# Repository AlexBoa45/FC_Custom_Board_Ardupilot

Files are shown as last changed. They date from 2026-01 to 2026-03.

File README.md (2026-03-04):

# Master Thesis Project, UPC-EETAC: 
# Design and development of the control PCB for a drone with a study of potential space applications

By: Alejandro Boadella

# Content

This TFM (project) is devoted to learning, exploring and expanding knowledge of the basic components essential for creating autonomous devices.

Control and power distribution boards are critical subsystems in unmanned vehicles. This project focuses on the complete design process of a dedicated drone control PCB. Furthermore, it includes a study of potential space applications and their specific technical requirements.

The principal objectives of this TFM are:

- Develop a functional drone control PCB.
- Create the drivers to manage the drone control PCB with ArduPilot.
- Evaluate the current design and expose space requirements.

TFE-Alejandro_Boadella.pdf is the main development document created.

**All the objectives have been accomplished. This project was developed over 5 months and involved the design of my very first PCB. The result is a fully functional PCB that can be used in a drone and has been successfully ported to the ArduPilot firmware. The magnetometer and MicroSD capabilities are not yet functional and require further improvement; however, the remaining sensors and system capabilities are fully operational. The microSD is most probably not operational due to hwdef file definition issues and poor routing, and the magnetometer is not operational due to manufacturer-related problems.**

This repository contains all the documentation developed during the TFM. All the design has been developed in Altium. BOM, CPL, Gerber, Master thesis and additional files can be found in this repository.

***IMPORTANT: TFE-Alejandro_Boadella.pdf schematics (shown pictures) and BOM file contain old HSE clock (incompatible with Ardupilot), functional flight controller version carries ASEMB-24.000MHZ-LC-T HSE clock, not SIT1602-22-33E-26.000000D. Both clocks contain same package. A simple susbtitution is required in BOM for manufacturing. TFE-Alejandro_Boadella.pdf explains this problem too.***

NOTE: the explanation of how to port a custom PCB flight controller to ArduPilot, development of a boards, space analysis and more can be found in the thesis.

## Simple Ardupilot Porting

Watch the video (https://www.youtube.com/watch?v=VTwxMDwfPzs)

## Simple Hardware Explanation

Watch the video (https://www.youtube.com/watch?v=8rlyB9k72sw)

## Here down below, you can see a few images from the developed project:





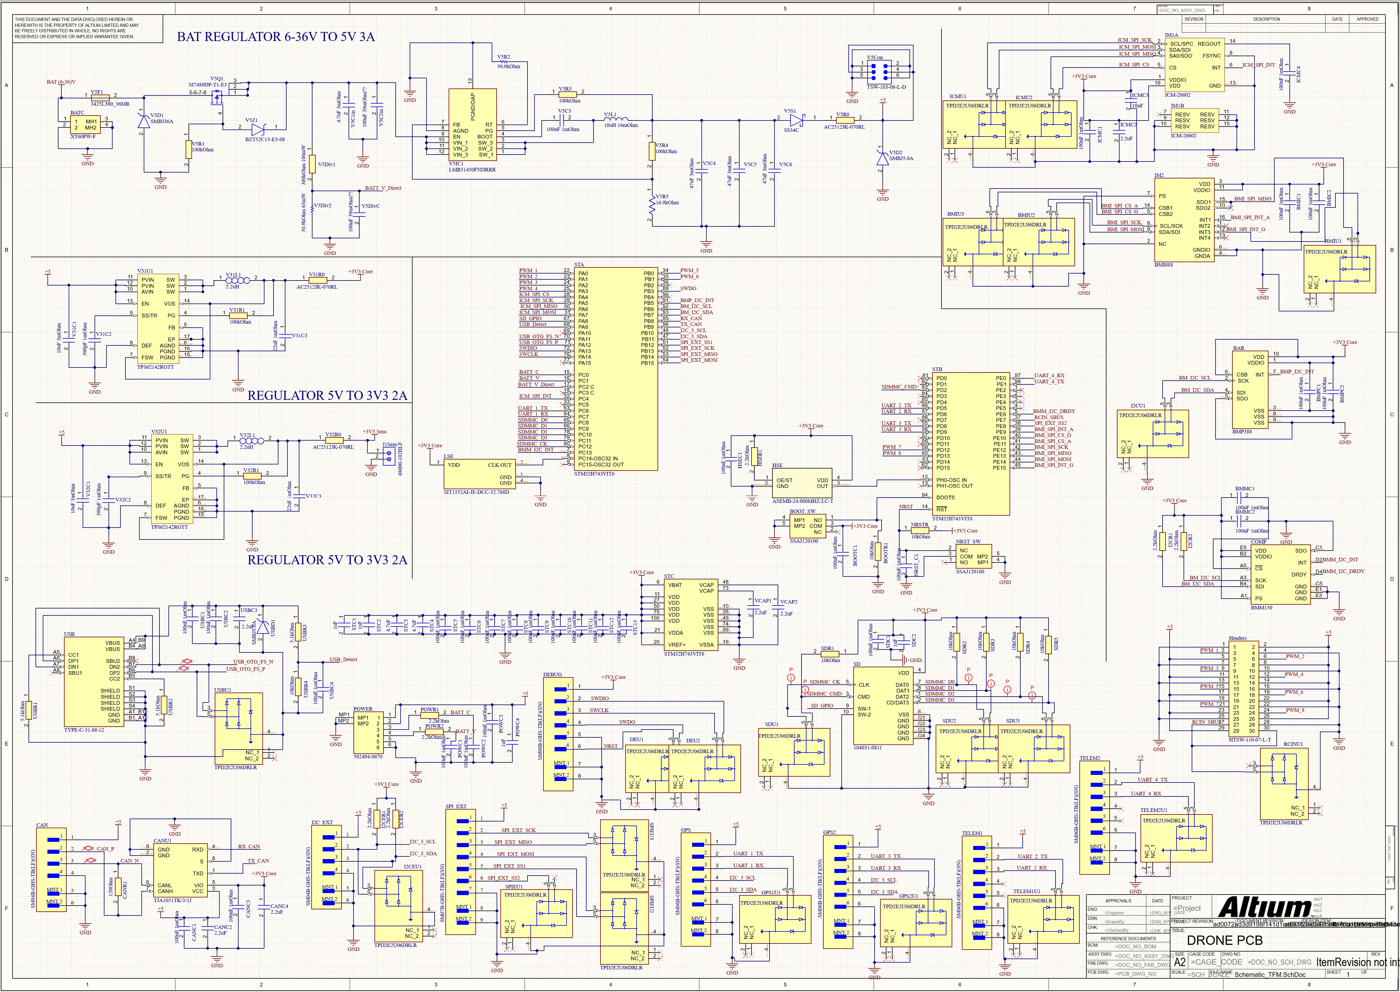
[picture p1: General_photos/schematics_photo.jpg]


## Tests: (autonomous flight has been tested and it actually work, no video has been done tho)

Watch the video (https://youtu.be/3_edOLgjn7w)

Watch the video (https://youtu.be/a62x8s5vOFY)

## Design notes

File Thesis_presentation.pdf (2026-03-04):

# Design and development of the control PCB for a drone with a study of potential space applications

Master's degree in Aerospace Science and Technology (MAST)

Boadella Aguado, Alejandro

Advisor:
- UPC: Oscar Casas Piedrafita
Academic support:
- UPC: Francisco Javier Lopez Garcia and Miguel Valero Garcia

# Index

### 1. Objectives and schedule

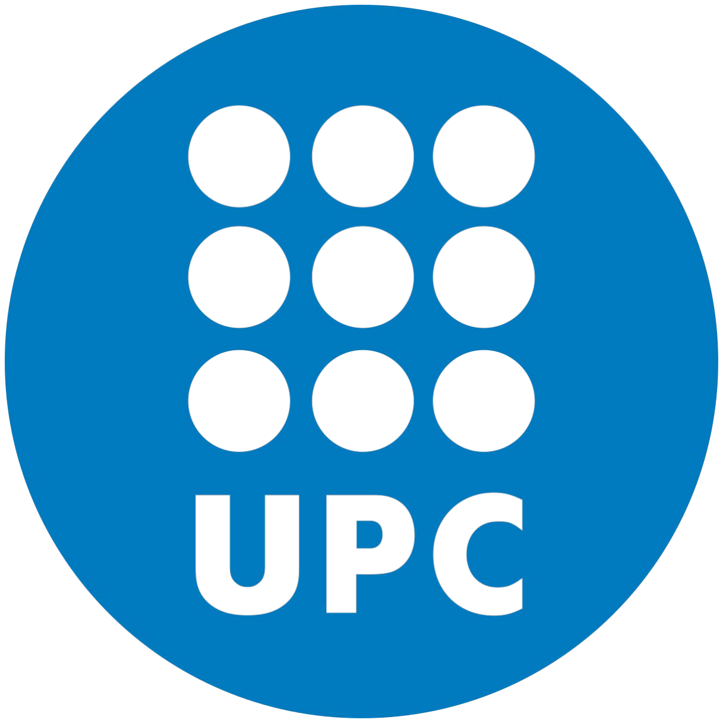
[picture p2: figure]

### 2. Intro and PCB Schematics 3. PCB Routing 4. Manufacturing and PCBA Files 5. Software Porting 6. Space Overview and application 7. Testing 8. Comparison 9. Cost and environment 10. Conclusions

# 1 - Objectives and schedule

# 1 - Objectives and schedule

### - Objectives of the TFM:

- Develop a functional drone control PCB.
- Create the drivers to manage the drone control PCB with ArduPilot.
- Evaluate the current design and expose space requirements.

# 1 - Objectives and schedule

- Example of commercial drone control PCB.

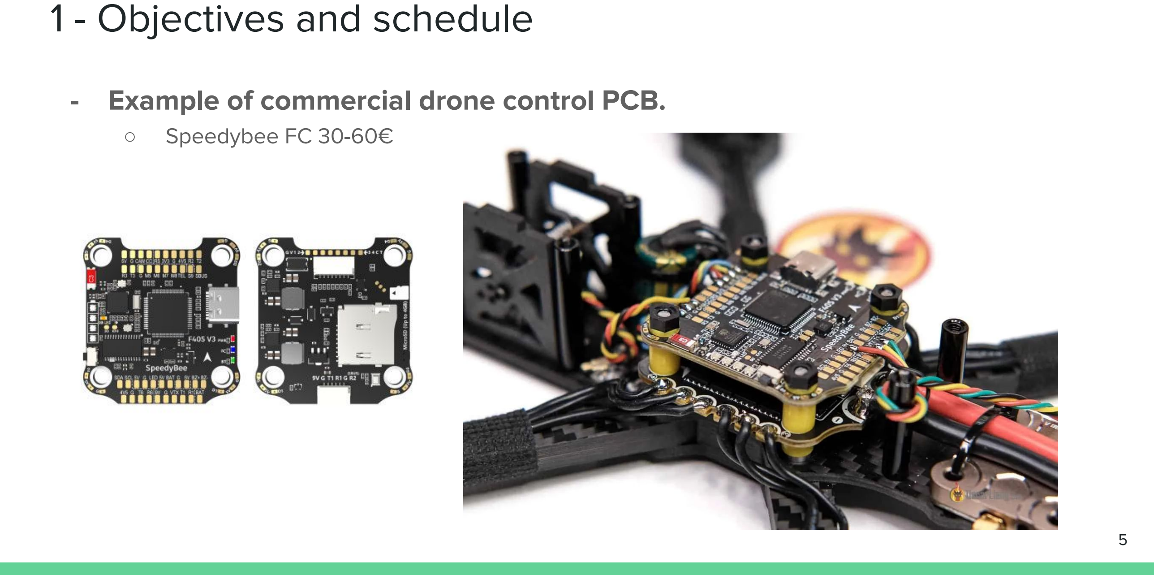
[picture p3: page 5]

- Speedybee FC 30-60€

# 1 - Objectives and schedule

### - Other examples:

- OpenPilot Revolution 60€
- Matek FC H743 70-110€
- Pixhawk 60-100€
- CubePilot Cube Orange/+ 350-600€
- CUAV X7 PRO+ 860€
- Makerfire UTMSYS USX51 600-1000€
OpenPilot | Matek | 6 Pixhawk | CUAV X7
CubePilot | Makerfire

# 2- Introduction

### - Basic components of a FC:

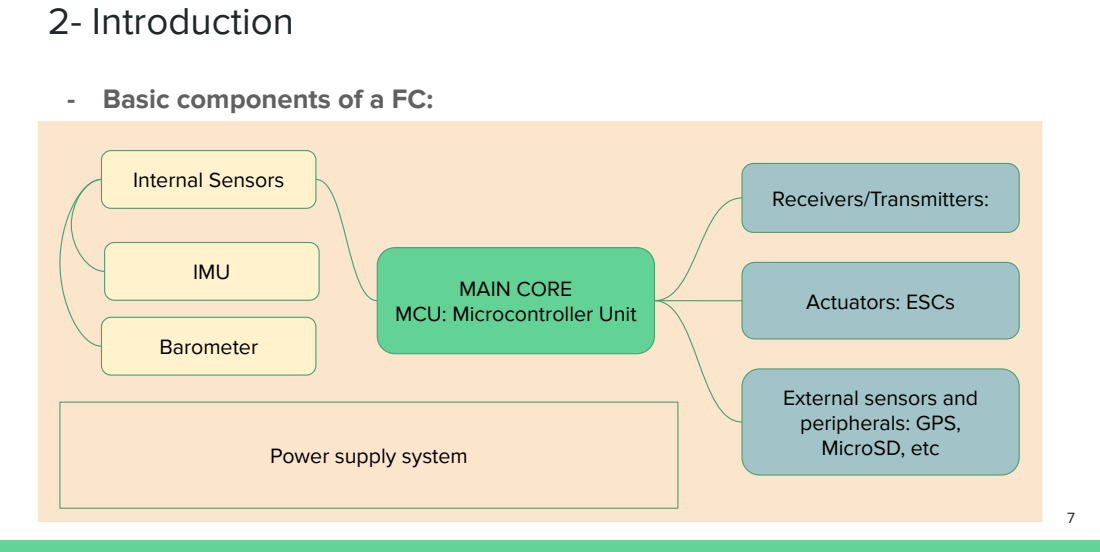
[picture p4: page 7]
Internal Sensors; Receivers/Transmitters:; Actuators: ESCs; IMU; Barometer

MAIN CORE
MCU: Microcontroller Unit

External sensors and
peripherals: GPS,
MicroSD, etc

Power supply system

# 2 - PCB Schematics

### - Before component selection:

- Drone Software: Ardupilot (professional firmware) → relies on ChibiOS.
- ChibiOS is a RTOS (Real Time Operating System).
■ IMPORTANT: Not all sensors and MCUs are supported by default.
- Drone Standard: Pixhawk Standard
■ Pixhawk connector-bus standard applied

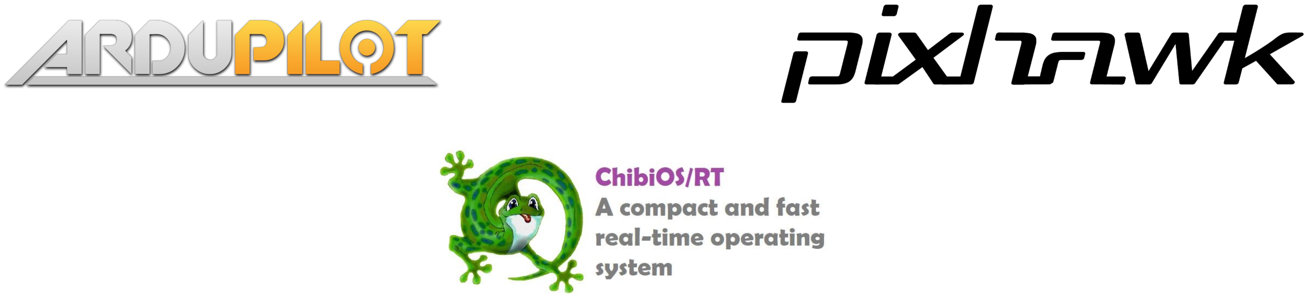
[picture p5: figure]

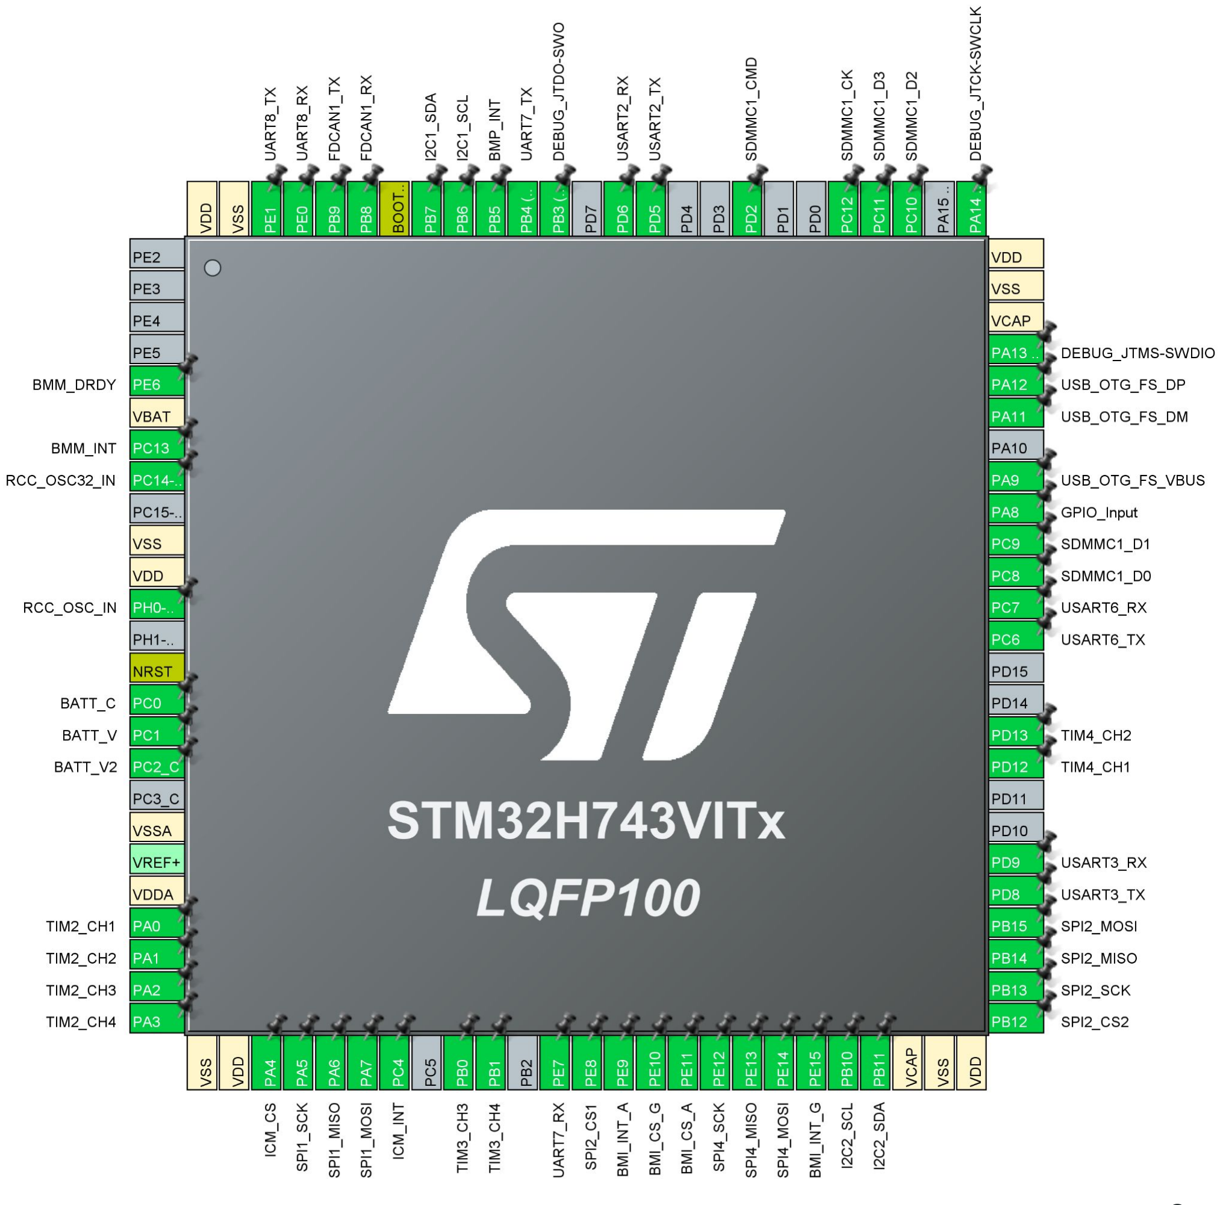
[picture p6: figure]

2 - PCB Schematics - MCU: - | High performance MCU: STM32H743VIT6 ■ | ARM-M7 RISC 480 MHz ■ | 2 MB Flash, 1 MB RAM ■ | LQFP100 (80/100 pins used) ● | 3 SPI (2 internal) ● | 1 SDMMC ● | 2 I2C (1 internal) ● | 3 ADCs (1 internal) ● | 8 PWM ● | 1 CAN ● | 1 USB ● | 1 SWD ● | 4 UART ● | MCU power connections

# 2 - PCB Schematics

### - MCU clock and schematics:

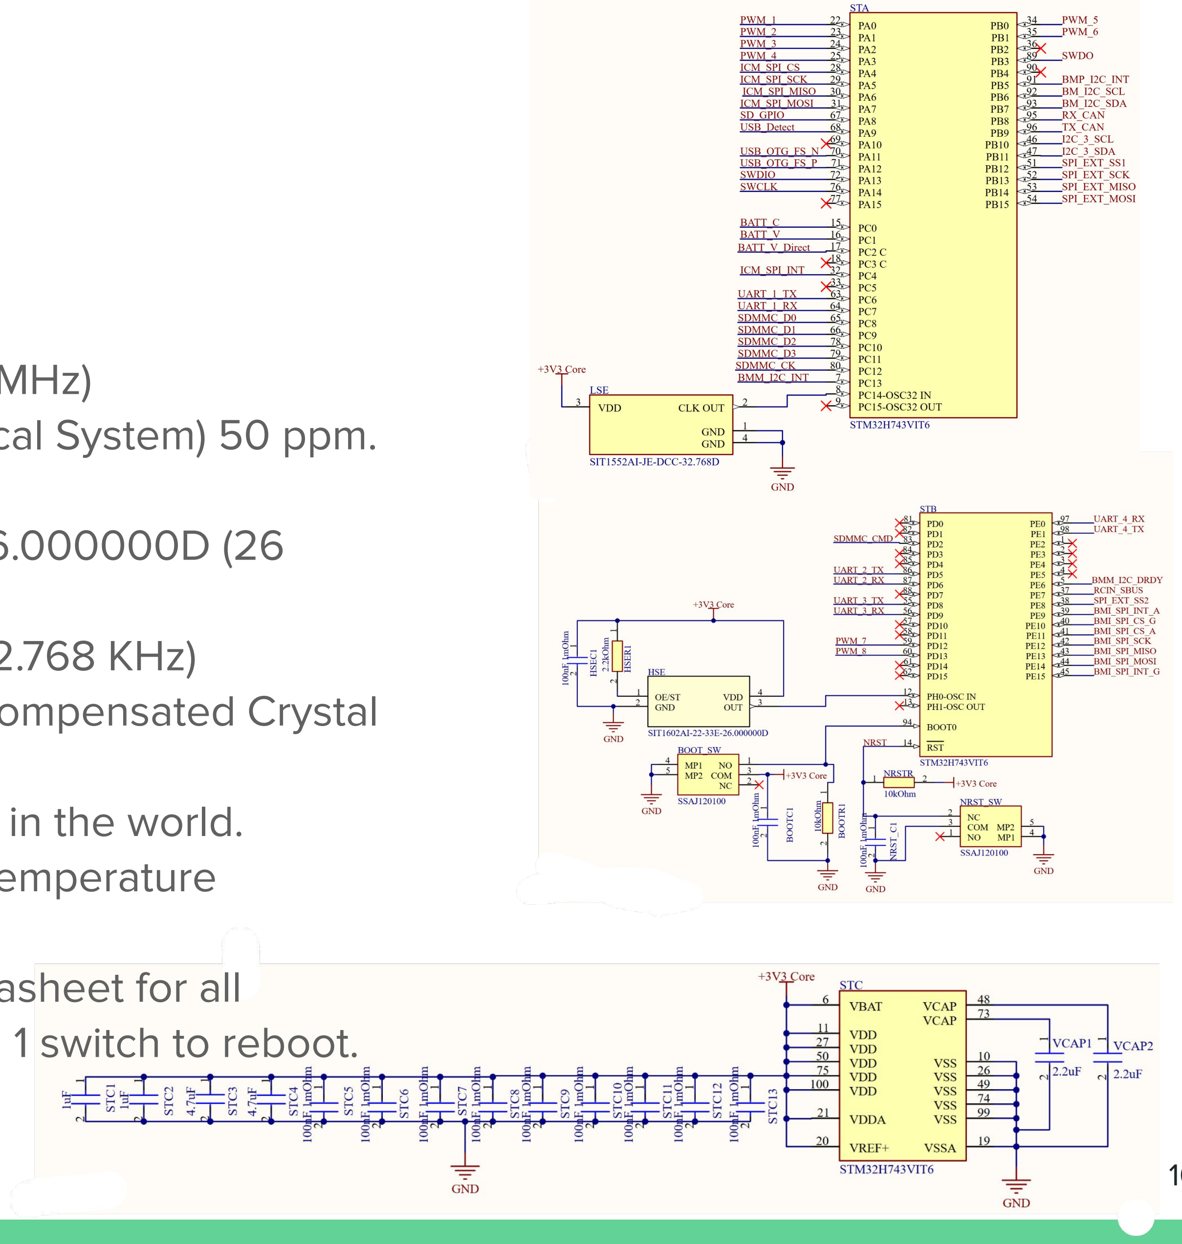
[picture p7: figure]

- HSE: ASEMB-24.000MHZ-LC-T (24 MHz)
■ | MEMS (Micro ElectroMechanical System) 50 ppm.
■ | Good against vibrations.
■ | Previously SIT1602-22-33E-26.000000D (26
| MHz).
- LSE: SIT1552AI-JE-DCC-32.768D (32.768 KHz)
■ | MEMS+TCXO (Temperature Compensated Crystal
| Oscillator) 5 ppm.
■ | Smallest programmable clock in the world.
■ | Good against vibrations and temperature
| variations.
- Conditioning specified as in the datasheet for all components. 1 switch for BOOT and 1 switch to reboot.

# 2 - PCB Schematics

### - Sensors:

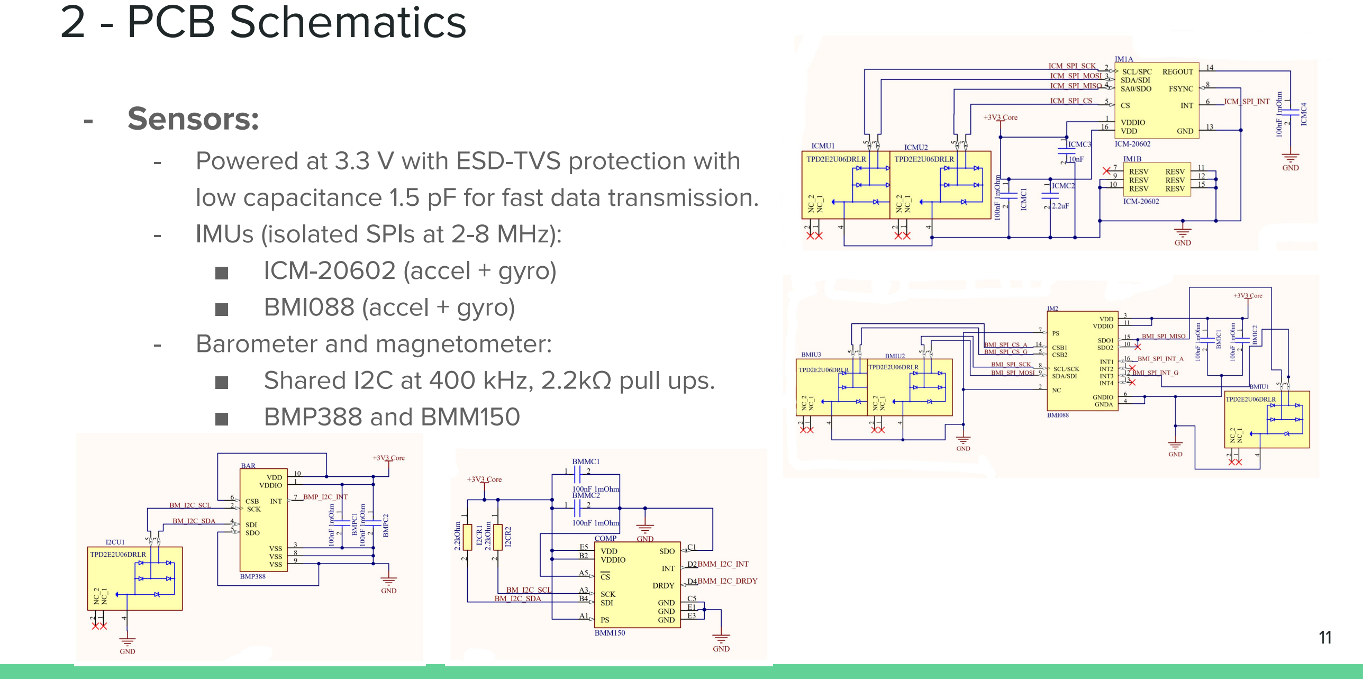
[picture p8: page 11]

- Powered at 3.3 V with ESD-TVS protection with low capacitance 1.5 pF for fast data transmission.
- IMUs (isolated SPIs at 2-8 MHz):
■ | ICM-20602 (accel + gyro)
■ | BMI088 (accel + gyro)
- Barometer and magnetometer:
■ | Shared I2C at 400 kHz, 2.2kΩ pull ups.
■ | BMP388 and BMM150

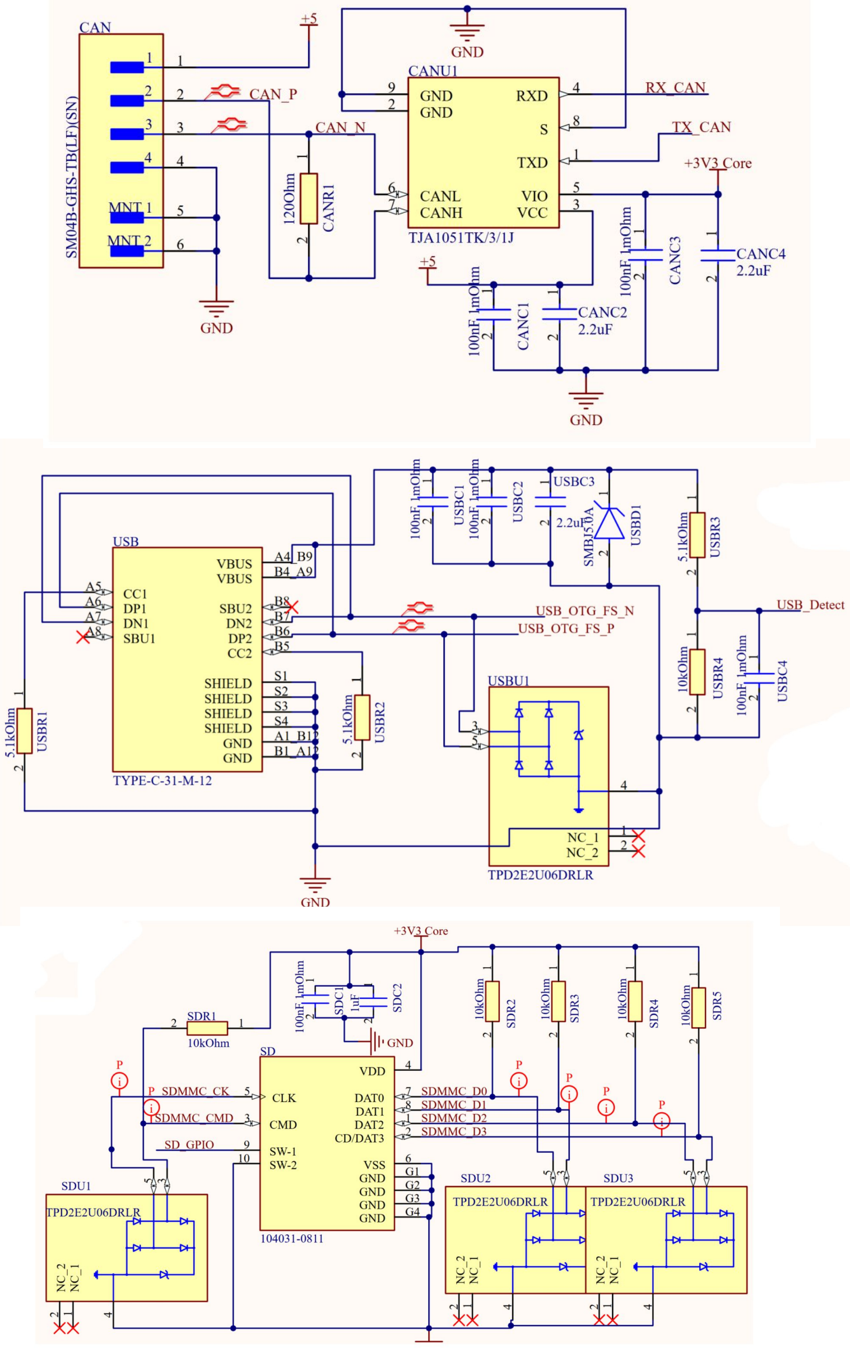
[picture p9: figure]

# 2 - PCB Schematics

### - Complex buses/connectors:

- CAN:
■ | 120 Ω
■ | Pixhawk connector SM04B-GHS JST.
■ | TJA1051TK/3/IJ transceiver (allows 3V3).
- USB 2.0 FS:
■ | 90 Ω
■ | 5.1 kΩ for termination device.
■ | ESD protection + filtering + detection line.
■ | It does not provide power source.
- SDMMC (MicroSD):
■ | 10 kΩ pull ups, except on CK line
■ | ESD protection + filtering + detection line.

# 2 - PCB Schematics

### - Other buses and connectors:

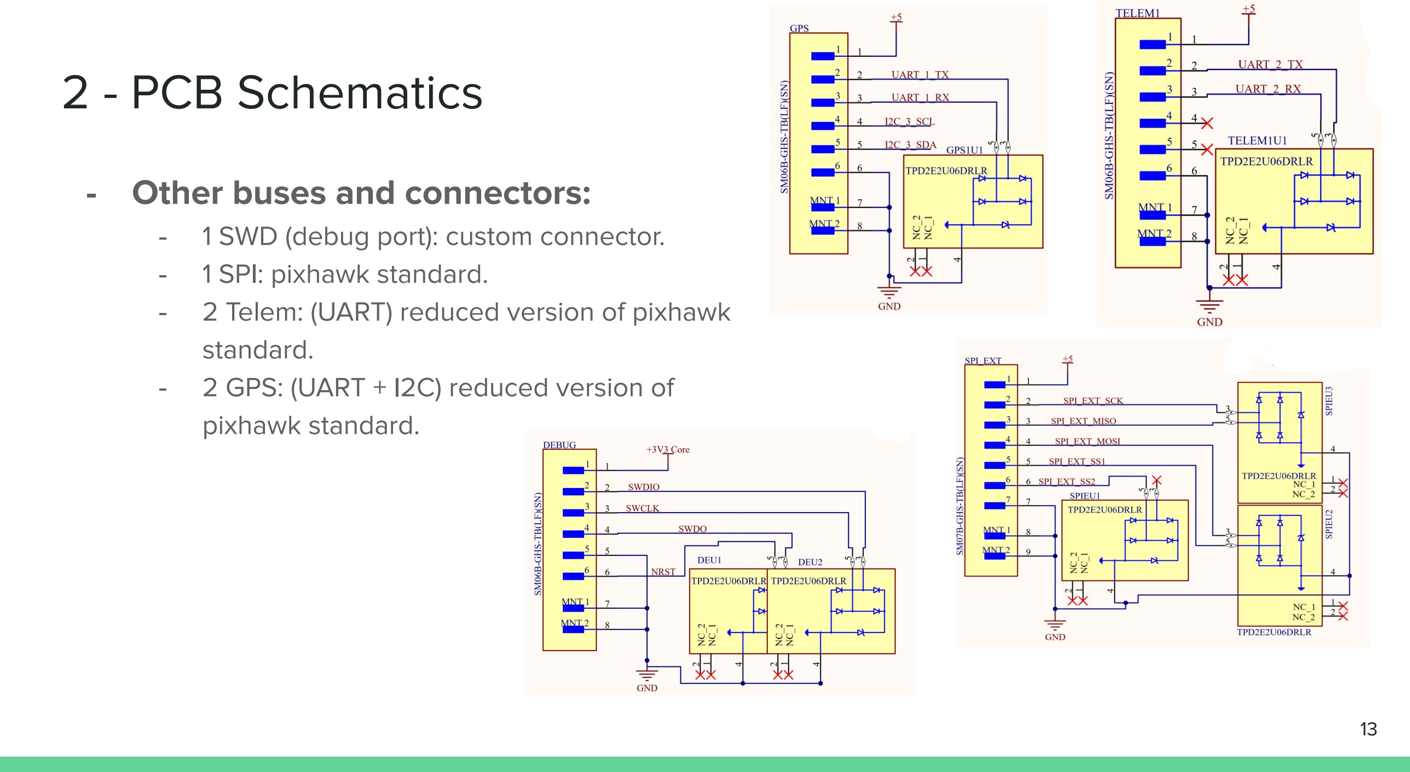
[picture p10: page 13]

- 1 SWD (debug port): custom connector.
- 1 SPI: pixhawk standard.
- 2 Telem: (UART) reduced version of pixhawk standard.
- 2 GPS: (UART + I2C) reduced version of pixhawk standard.

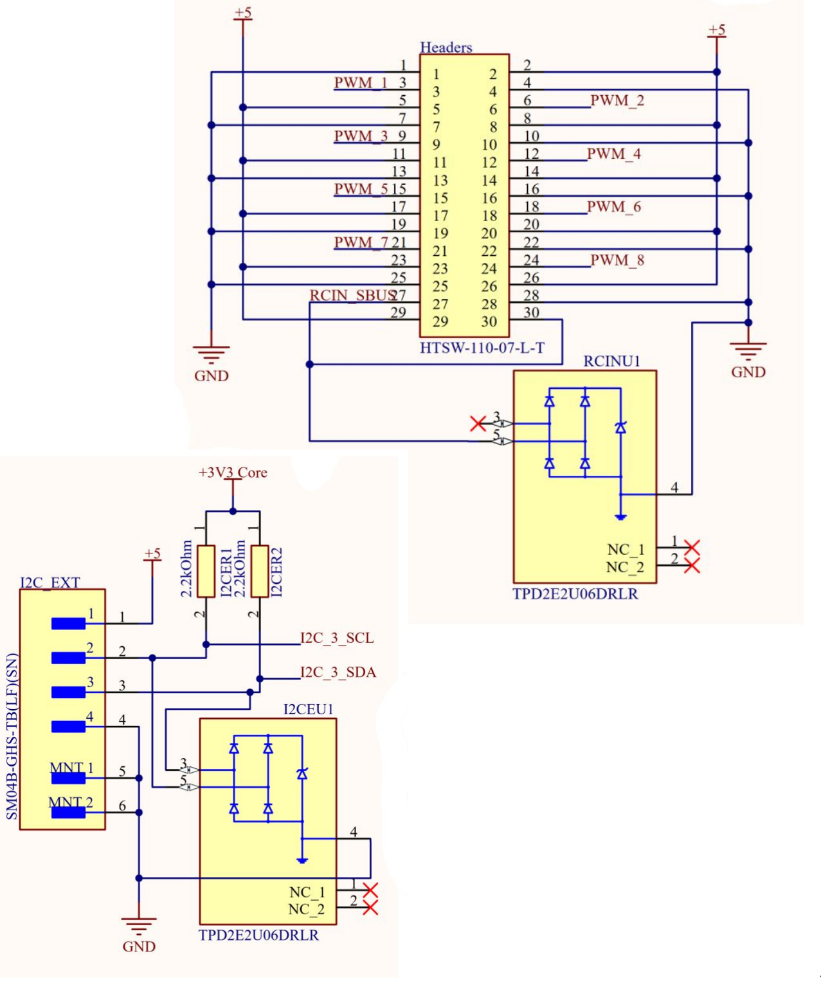
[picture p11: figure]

# 2 - PCB Schematics

### - Other buses and connectors:

- 1 I2C: pixhawk standard.
- 2.54 mm pitch headers/pins:
■ | 8 PWM (No ESD protection and no
| resistance in serie)
■ | 1 RCIN conector (UART RX) (admits
| SBUS with internal inversion).

# 2 - PCB Schematics

### - Power supply system:

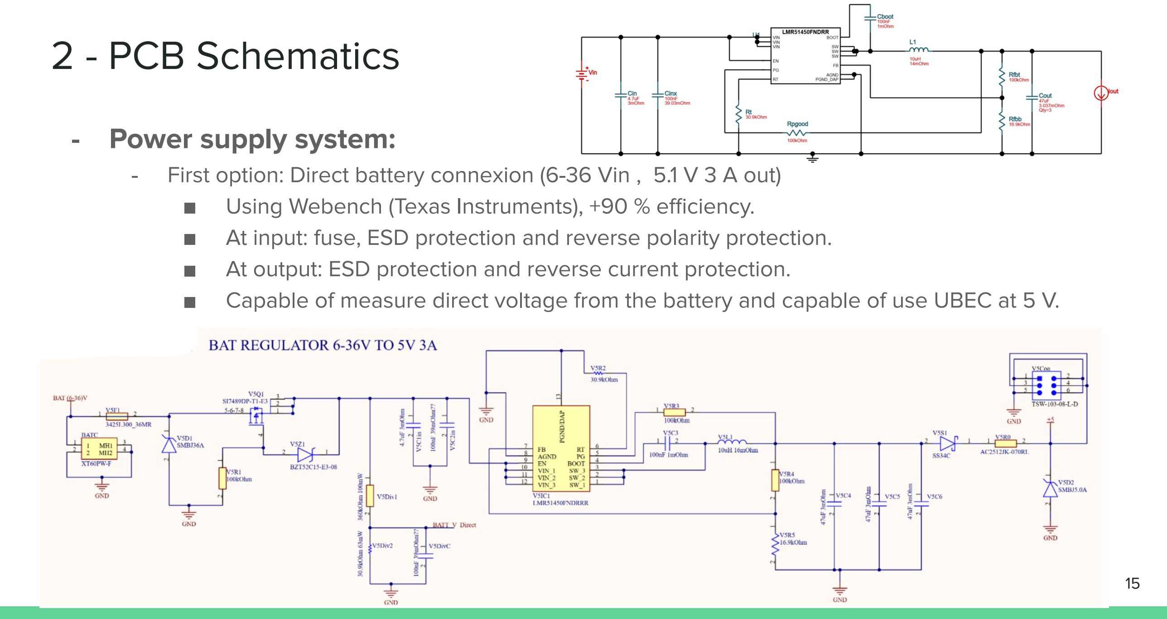
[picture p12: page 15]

- First option: Direct battery connexion (6-36 Vin , 5.1 V 3 A out)
■ | Using Webench (Texas Instruments), +90 % efficiency.
■ | At input: fuse, ESD protection and reverse polarity protection.
■ | At output: ESD protection and reverse current protection.
■ | Capable of measure direct voltage from the battery and capable of use UBEC at 5 V.

# 2 - PCB Schematics

### - Power supply system:

- Second option: Pixhawk battery connexion port
■ | 5.3 V at 2.5 A (real values are near 5.4 V).
■ | Filtered.
■ | Capable of measure current and voltage from external block.

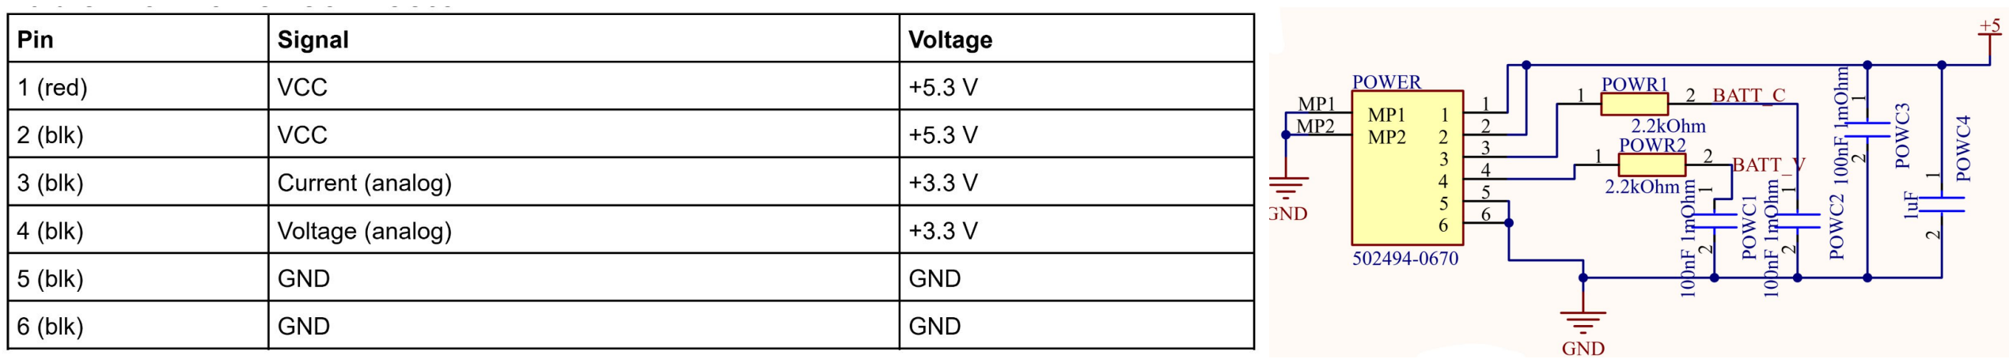
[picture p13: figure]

# 2 - PCB Schematics

### - Power supply system:

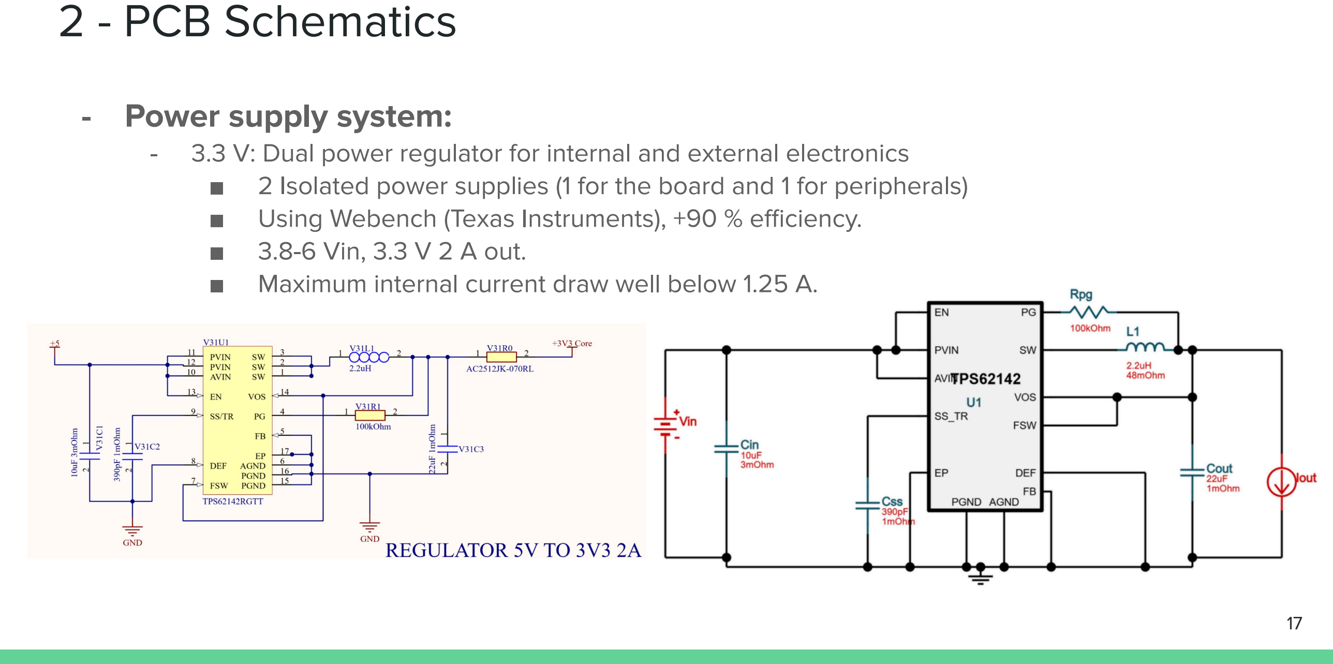
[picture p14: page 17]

- 3.3 V: Dual power regulator for internal and external electronics
■ | 2 Isolated power supplies (1 for the board and 1 for peripherals)
■ | Using Webench (Texas Instruments), +90 % efficiency.
■ | 3.8-6 Vin, 3.3 V 2 A out.
■ | Maximum internal current draw well below 1.25 A.

# 3 - PCB Routing

### - Layer Stackup JLCPCB:

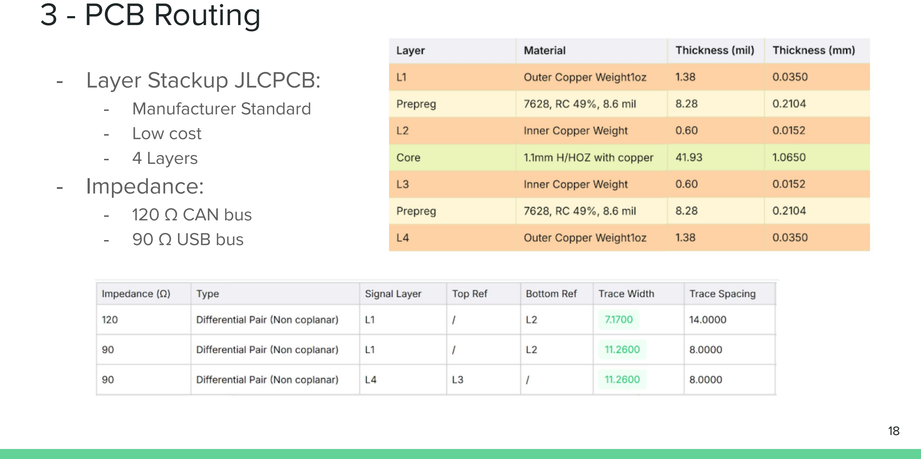
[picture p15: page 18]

- Manufacturer Standard
- Low cost
- 4 Layers

### - Impedance:

- 120 Ω CAN bus
- 90 Ω USB bus

# 3 - PCB Routing

### - Planes and trace width IPC-2152:

- L1: Signal and power lines
- L2: GND → reference plane
- L3: Power (5V and 3V3) and GND → reference
- L4: Signal

# 3 - PCB Routing

### - Power lines:

- Following datasheet routing.

### - Sensors and MCU:

- BMM150 copper pour.
- Capacitors near MCU.
- BMI088, merge MISO lines.
■ Problematic on high-freq.

# 3 - PCB Routing

### - Special buses:

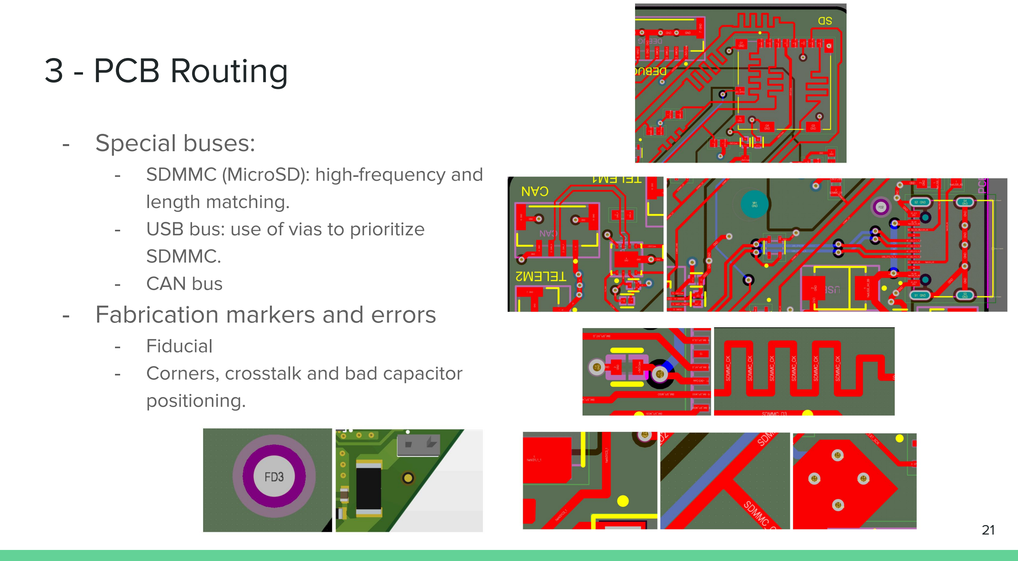
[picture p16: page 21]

- SDMMC (MicroSD): high-frequency and length matching.
- USB bus: use of vias to prioritize SDMMC.
- CAN bus

### - Fabrication markers and errors

- Fiducial
- Corners, crosstalk and bad capacitor positioning.

# 4 - Manufacturing and PCBA Files

- Manufacturer most stringent capability and verification:
- Trace width 4 mil +-20 % (39.37 mil = 1 mm) (specially for magnetometer)
- Un-plug vias for testing and 0402 min size to reduce cost.
- Always checking DFM (Design For Manufacturability).
■ Altium design rule checker and/or Manufacturer programme.
- Actual JLCPCB trace positioning deviation <1 mil. No solderwicking, nor soldebridging.
- Some vias plugged with solder due to HASL bath.

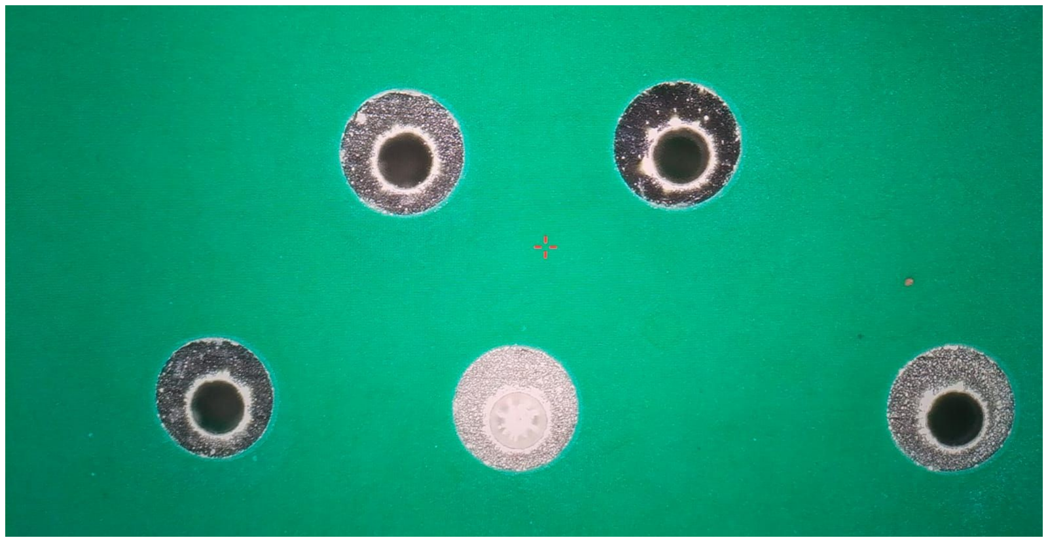
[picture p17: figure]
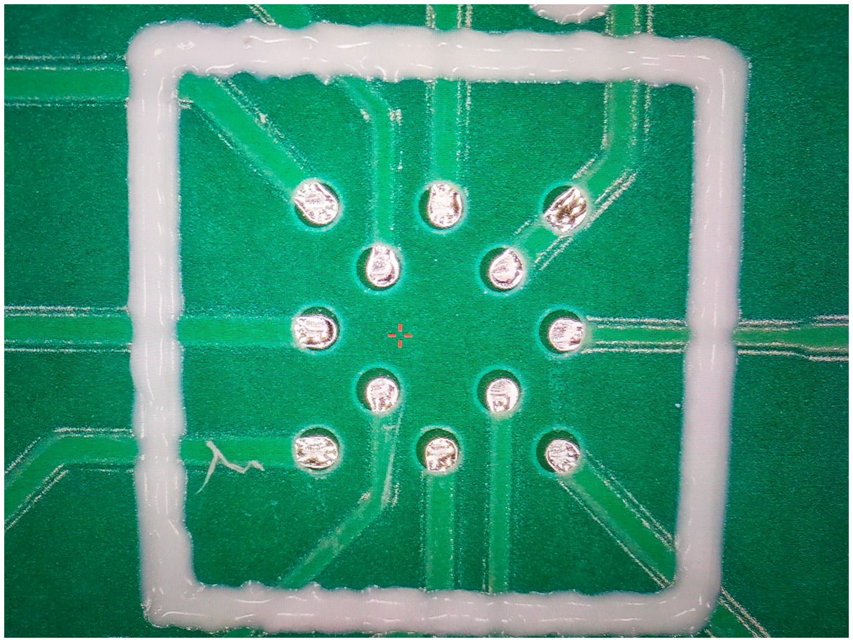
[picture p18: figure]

- Files:
- Gerber X2
- CPL (or PnP): Customized (wrong rotations).
■ 146 components per board.
- BOM: Customized (Manufacturer part number + PCB manufacturer number) ■ 44 different components per board (in fact 50 considering non-used).

# 5 - Software Porting

### - Environment installation:

- Linux and Ubuntu
- Download ArduPilot
- Install ArduPilot and ChibiOS
- Update them

### - Create a folder and add hwdef.dat and hwdef-bl.dat

files.

### - Create the firmware and the

bootloader.

wsl --install
wsl --install -d Ubuntu
sudo apt update && sudo apt install git -y

git clone https://github.com/ArduPilot/ardupilot.git

cd ardupilot
git submodule update --init --recursive Tools/environment_install/install-prereqs-ubuntu.sh -y . ~/.profile

cd ardupilot/libraries/AP_HAL_ChibiOS/hwdef

cd ~/ardupilocd
ardupilot/libraries/AP_HAL_ChibiOS/hwdeft ./Tools/scripts/build_bootloaders.py CustomH7 ./waf configure --board CustomH7
./waf copter

# 5 - Software Porting

- 2 MB in order:
- Divided in 16 pages of 128 KB
- Bootloader 128 KB
- Dedicated storage 32 KB
- Firmware + addons 1888 KB
- hwdef.dat and hwdef-bl.dat files:
- Test-fail-read_doc-try_again
- PLL with 26 MHz HSE:
- In STM32cubeIDE impossible with auto-mode, possible with manual mode with multipliers/dividers.
- ChibiOS needs 24 MHz , (Impossible to interact with manual PLL values at 26 Mhz, I tried, plausible reason→USB 48 Mhz), (replacement!!).

# Core

MCU STM32H7xx STM32H743xx
FLASH_SIZE_KB 2048
FLASH_RESERVE_START_KB 128 …
# Clock

OSCILLATOR_HZ 24000000
STM32_HSE_BYPASS
STM32_LSE_BYPASS
STM32_SYSCLK 400000000
STM32_ST_USE_TIMER 5
…
# Pins and timers to provide high speed data, even Dshot PB8 CAN1_RX CAN1

PA0 TIM2_CH1 TIM2 PWM(1) GPIO(50)
…
# Order of buses: (0, 1, 2, 3, 4, 5, ..)

SERIAL_ORDER OTG1 USART6 USART2 USART3 UART7 UART8 …
# Sensor bus speed definition range

SPIDEV icm20602 SPI1 DEVID1 ICM_CS MODE3 2*MHZ 8*MHZ …
#Sensor drivers and rotation

IMU Invensense SPI:icm20602 ROTATION_YAW_90
…
# System PID page storage and size to store values STORAGE_FLASH_PAGE 14

define HAL_STORAGE_SIZE 32768
…
# Bus DMA priority (in fact 2 DMAs using DMAMUX) DMA_PRIORITY SPI1* SPI4* CAN1* SDMMC* USART6*

# 5 - Software Porting

### - ArduPilot proposes dfu-utils and the process of porting is not very clear, so:

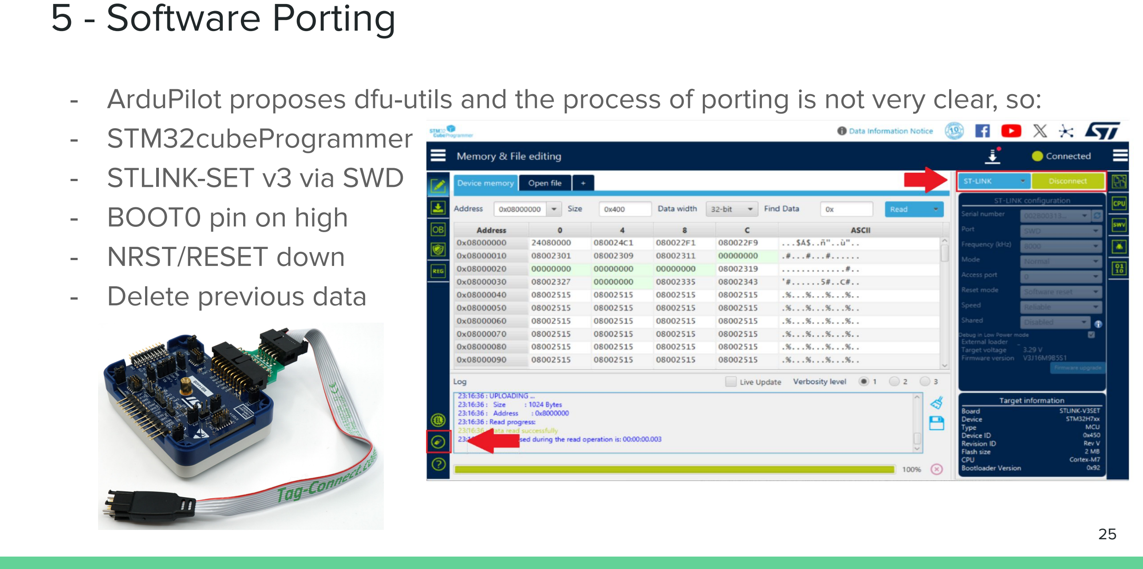
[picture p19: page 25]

### - STM32cubeProgrammer - STLINK-SET v3 via SWD - BOOT0 pin on high - NRST/RESET down - Delete previous data

# 5 - Software Porting

### - Delete previous data

### - Open the generated code arducopter_with_bl.hex

- At: ardupilot/build/CustomH7/bin/

### - Upload code at: 0x0800 0000

- Lastly reboot the board and BOOT0 pin down.

# 6 - Space Overview and application

- Possible applications for drones in space.
- ISS (inside): monitor data, evaluate the environment, and assist with daily tasks. ■ Problem → Microgravity (temperature).
- MARS: transport of goods, mapping, data relay, differential positioning, etc.
■ Problem → Low air density, and extreme temperature.
- VENUS: similar applications compared to MARS.
■ Problem → Extreme pressure, temperature and corrosion. Feasible at high altitudes.
- TITAN: similar applications compared to MARS.
■ Problem → Quite feasible, though low temperature.
- Other mandatory considerations: radiation, outgassing, vibrations, shocks, etc.

# 6 - Space Overview and application (SPENVIS)

### - Simple radiation analysis of STM32H743VIT, COTS, 2 year mission:

- With ECSS RDM (Radiation Design Margin) of 2, and TID of 47 krad from STM32H753
- SSO (Sun-Synchronous Orbit) 700 km → 0.5 mm approx minimum of Al protection.
- MARS at 100 km from surface → 0.02 mm approx minimum of Al protection.

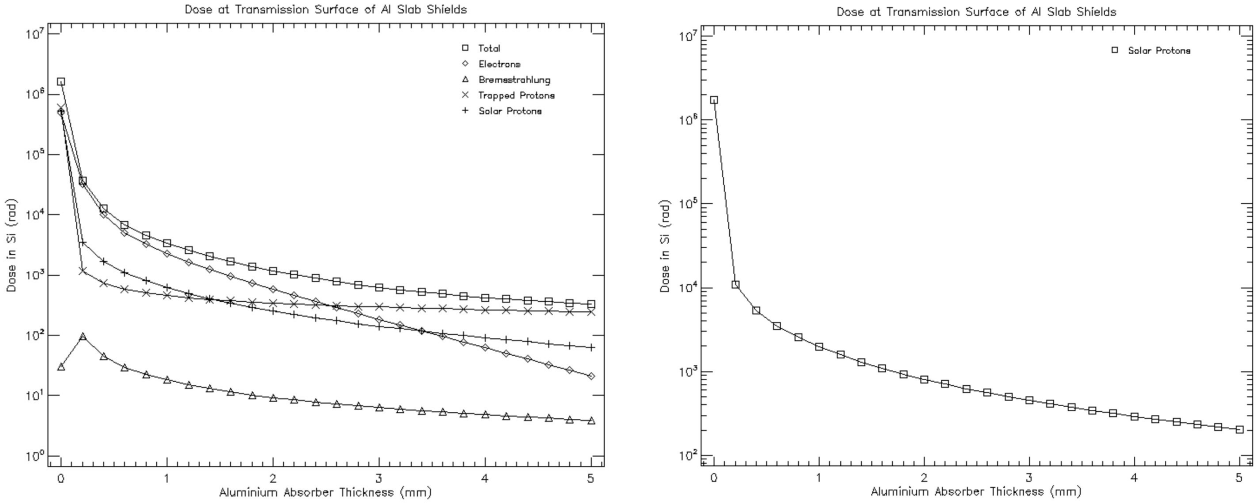
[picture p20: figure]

# 6 - Space Overview and application (SPENVIS)

### - Simple radiation analysis of STM32H743VIT, COTS, 2 year mission:

- 40 nm technology on SRAM → 0.2 µm x 0.2 µm x 0.2 µm sensitive volume approx
- 1 MB RAM contains 8388608 bits
- SSO:
■ | Long-term (SEU):
| ● 2 mm of Al 910 errors, 4 mm of Al 246 errors
■ | Short-term (SEU):
| ● 2 mm of Al 1653 errors, 4 mm of Al 451 errors
- MARS:
■ | Long-term (SEU):
| ● 2 mm of Al 2858 errors, 4 mm of Al 761 errors
■ | Short-term (SEU):
| ● 2 mm of Al 3235 errors, 4 mm of Al 614 errors

### - SSO requires more Al protection while MARS requires more active mitigation

and redundancy.

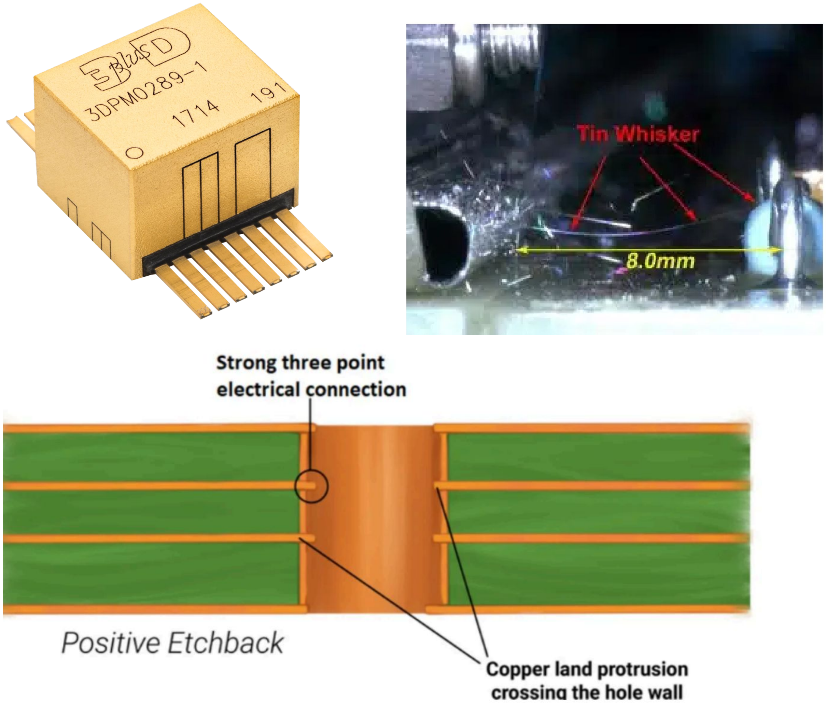
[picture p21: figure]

6 - Space Overview and application - Multiple Standards analyzed: - | IPC, MIL-STD, NASA, ECSS. - Current COTS components considerations: - | Derating and staking. - | Bake-out campaign (outgassing). - | Temperature, pressure, rad, vibration, shock tests. - | LCL (Latch-up Current Limiters). - | High Tg materials, with symmetric PCB. - | SnPb (Tin whiskers) (solder and PGA/BGA/LGA). - | ENIG (Electroless Nickel Immersion Gold). - | ESD protection and positive etchback. - | Special coating against arcing or corona effect. - | Other: If possible Flip-chip package with PIND

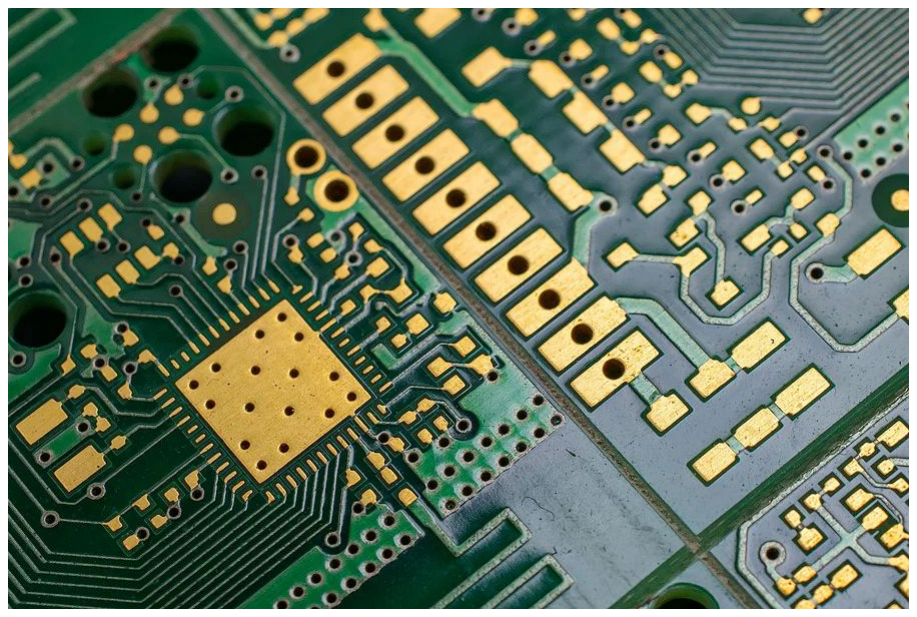
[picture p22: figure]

(Particle Impact Noise Detection) test.

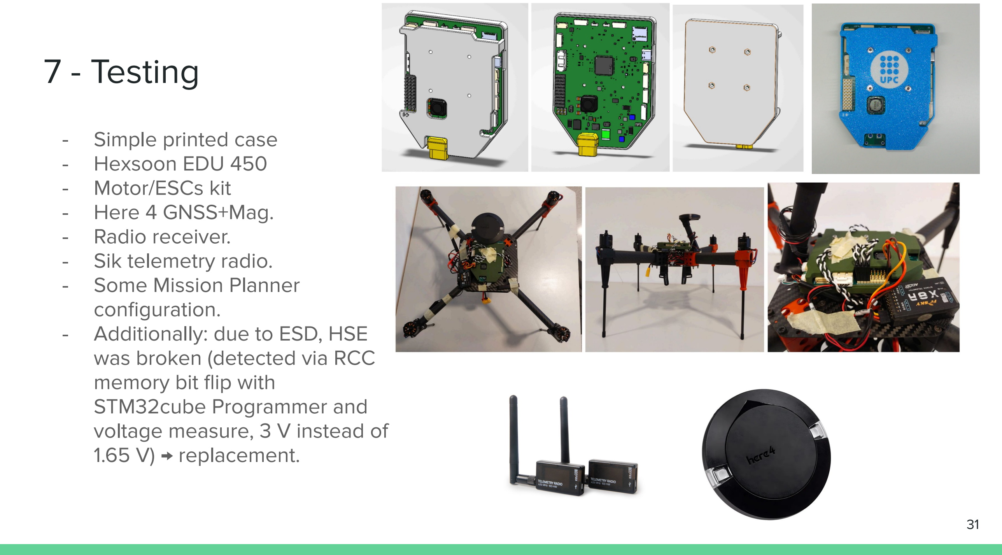
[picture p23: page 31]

7 - Testing - Simple printed case - Hexsoon EDU 450 - Motor/ESCs kit - Here 4 GNSS+Mag. - Radio receiver. - Sik telemetry radio. - Some Mission Planner

configuration.
- Additionally: due to ESD, HSE was broken (detected via RCC memory bit flip with
STM32cube Programmer and
voltage measure, 3 V instead of 1.65 V) → replacement.

# 7 - Testing

### - 3 main tests:

- Drone anchored.
- Drone inside a geofence.
- Autonomous mission.

### - All tests were performed

successfully.

### - Remaining issues:

- SDMMC inactive.

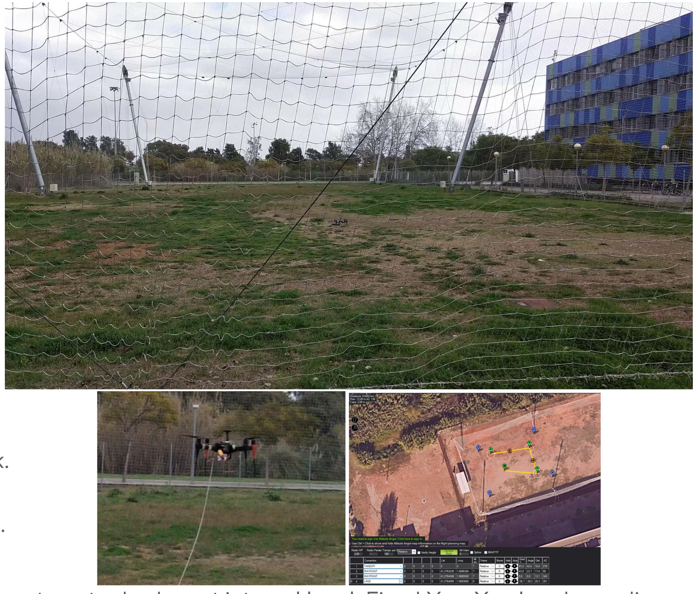
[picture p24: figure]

■ Check hwdef or crosstalk.
- Noisy internal magnetometer. ■ PCB design → Impossible.
- Advanced ESD protection and redundancy.
- Both magnetometer broken at internal level. Fixed Y or X value depending
| on the board, possible reason → Manufacturing or stress.

# 8 - Comparison

### - Designed board:

- Bridge between professional and hobbyist flight controller.
- Pros:
■ | High computational capability. Small and powerful STM32H7 (480 MHz).
■ | Pixhawk connectivity. JST-GH.
■ | Advanced electrical protection (ESD, reverse current, advance regulators, fuse, etc).
■ | Precision timing architecture. MEMS/TCXO.
■ | Advanced firmware integration. ArduPilot porting.
- Cons:
■ | Legacy sensors but more reliable.
■ | No dedicated I/O co-processor.
■ | Lack of multiple peripherals.
■ | No PWM and ADC electrical protection. Lack of eFuse (LCL) on datalines.
■ | Size and weight 77g.

# 9 - Cost and environment

### - Cost:

- Prototype: 186.77 € per board
- 10 board production line: 65-70 € per board

### - Environment and social impact:

- All components are RoHS compliant.
- Project addresses SDG (Sustainable Development Goals):
■ | 9 - Industry, Innovation, and Infrastructure
■ | 4 - Quality Education

# 10 - Conclusions

### - All objectives have been completed:

1. Develop a functional drone control PCB.
2. Create the drivers to manage the drone control PCB with ArduPilot.
3. Evaluate the current design and expose space requirements.

### - Project value:

- Custom board porting:
■ | Unlike Betaflight, ArduPilot required defining a low-level architecture.
■ | Manually implemented the hwdef file to map STM32 resources to the ChibiOS.
- Full open-engineering project:
■ | Moving beyond the “Ardupilot Open Hardware” (limited to PDFs, hwdef, and in some quite
| rare cases, Gerber files).
■ | Providing methodology: calculations, impedance, routing, layer stack-up, Altium files and
| porting steps.
- Considerations:
■ | Designed from scratch using reference architectures + space considerations.
■ | Adapted circuits based on COTS stock availability and reduced cost.
■ | Validated the theoretical design in a functional prototype, all in 5 months.

# Thanks

# Improvements

### - Mandatory or mid-complex:

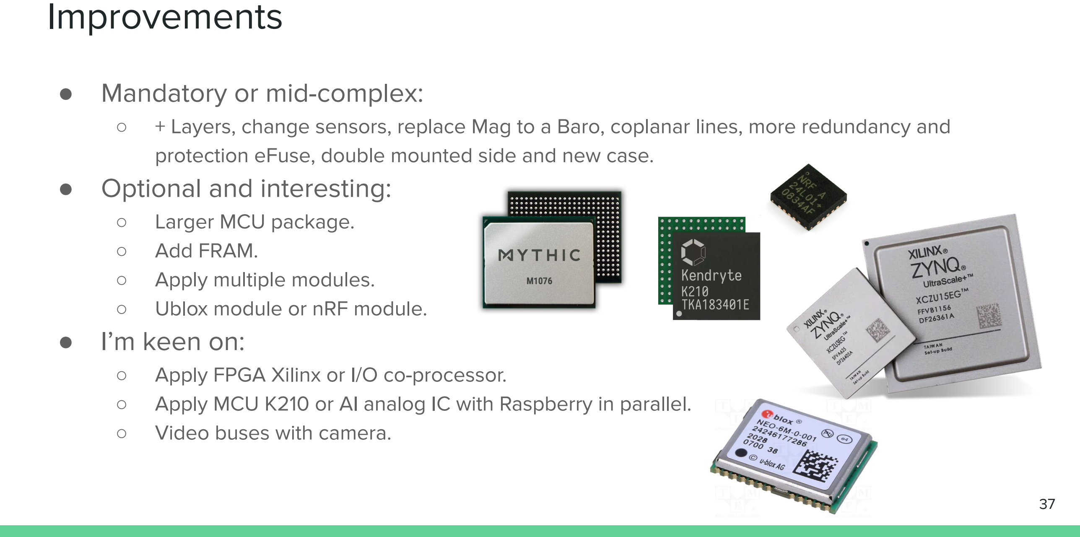
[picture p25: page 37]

- + Layers, change sensors, replace Mag to a Baro, coplanar lines, more redundancy and protection eFuse, double mounted side and new case.

### - Optional and interesting:

- Larger MCU package.
- Add FRAM.
- Apply multiple modules.
- Ublox module or nRF module.

### - I’m keen on:

- Apply FPGA Xilinx or I/O co-processor.
- Apply MCU K210 or AI analog IC with Raspberry in parallel.
- Video buses with camera.

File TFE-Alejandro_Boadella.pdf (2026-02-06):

# Design and development of the control PCB for a drone with a study of potential space applications

## Alejandro Boadella Aguado

SUPERVISED BY

Jaime Oscar Casas Piedrafita

WITH ACADEMIC SUPPORT FROM:

Francisco Javier Lopez Garcia Miguel Valero Garcia

Universitat Politècnica de Catalunya Master in Aerospace Science & Technology January 2026

## Design and development of the control PCB for a drone with a study of potential space applications

BY
Alejandro Boadella Aguado

DIPLOMA THESIS FOR DEGREE
Master in Aerospace Science and Technology

AT
Universitat Politècnica de Catalunya

SUPERVISED BY:
Jaime Oscar Casas Piedrafita Department of Electronics

WITH ACADEMIC SUPPORT FROM:
Francisco Javier Lopez Garcia Head of Research Electronics Laboratory

Miguel Valero Garcia
Department of Computational Architecture

## ABSTRACT

This project focuses on the development of a dedicated flight control PCB specifically optimized for multirotor systems.

The TFM begins with the design of a customized hardware platform using Altium Designer, WEBENCH and STM32CubeIDE. It explores design capabilities and alternatives by comparing against commercial and hobbyist flight controllers. The project then aims to perform PCB layer stack-up, impedance control, and routing strategies to ensure signal integrity, with the objective of generating industry-standard fabrication files.

Following the hardware development phase, the project moves into software integration. This consists of configuring the hardware and selecting pinouts to support the ChibiOS. Allowing the porting and execution of the ArduPilot firmware onto the custom hardware, using STM32CubeProgrammer for deployment.

Finally, the project evaluates the developed PCB components, with attention to the steps that could make the hardware suitable for space applications based on current space standards. This involves adaptations such as radiation tolerance, thermal management, and the use of components certified for operation in harsh environments.

## Table of Contents

A-1.2.5. Other systems: FPV and storage | 72
A-1.3. Example 2: PULPY_F405_FC | 73
A-1.3.1. MCU system | 73
A-1.3.2. Sensor and actuators | 74
A-1.3.3. Communication buses | 74
A-1.3.4. Power regulation system | 75
A-1.3.5. Other systems: Flash and LEDs | 75
A-1.4. Example 3: NxtPX4v2 | 76
A-1.4.1. MCU system | 76
A-1.4.2. Sensors | 77
A-1.4.3. Communication buses | 77
A-1.4.4. Power regulation system | 77
A-1.4.5. Storage | 78
A-1.4. Example 4: FC F4BY H743 | 79
A-1.5.1. MCU system | 79
A-1.5.2. Sensors | 80
A-1.5.3. Communication buses | 80
A-1.5.4. Power regulation system | 80
A-1.5.5. Storage | 81
ANNEX-2. SPACE ENVIRONMENT AND ELECTRONICS OVERVIEW | 82
A-2.1. Space Environment | 82
A-2.1.1. ISS: International Space Station | 82
A-2.1.2. MARS | 82
A-2.1.3. VENUS and TITAN | 83
A-2.2. Standards Introduction | 85
A-2.3. IPC Standards | 86
A-2.4. NASA Electronic Standards | 91
A-2.4.1. NASA-STD-8739 | 91
A-2.4.2. MIL-PRF-38535M | 94
A-2.4.3. EEE-INST-002 | 96
A-2.4.4. MIL-STD-883E (a few methods) | 96
A-2.4.5. NASA-STD-4005 | 97
A-2.5. ECSS-ESA Standards | 99
A-2.5.1. ECSS-E-ST-20C | 99
A-2.5.2. ECSS-Q-ST-70-12C | 100
A-2.5.3. ECSS-Q-ST-60C and ECSS-Q-ST-60-15C | 101
A-2.6. SEE and TID calculation (ECSS-E-ST-10-12C) | 103
ANNEX-3. TESTING, PROJECT ISSUES, COMPARISON AND COST | 108
A-3.1. Testing with Mission Planner | 108
A-3.1.1. Board case | 108
A-3.2.1. Drone construction and mission planner configuration | 109
A-3.1.1. Tests | 110
A-3.2. Resolved and remaining Issues | 111
A-3.2.1. Configuration, clock and ESD protection | 111

A-3.2.2. Storage and compass | 111
A-3.3. Comparison | 112
A-3.4. Improvements | 116
A-3.4.1. Easy short term improvements | 116
A-3.4.2. Medium long term improvements | 116
A-3.4.3. Complex improvements | 117
A-3.5. Cost evaluation | 117
ACRONYMS | 118
REFERENCES | 124
ADDITIONAL DOCUMENTATION | 131

## List of Figures

Fig. 2.10 Left→ CAN bus, Right→ USB FS bus | 27
Fig. 2.11 Fiducial | 27
Fig. 2.12 Left→ Analog measure traces, Center→ Decoupling, Right→ Accordion | 27
Fig. 2.13 Copper corners | 28
Fig. 3.1 STM32CubeProgrammer connection and memory delete | 33
Fig. 3.2 Uploading steps | 33
Fig. 4.1 LEO Shieldose-2 results | 42
Fig. 4.2 Fluence vs LET with 4 mm Al | 44
Fig. 4.3 Mars Shieldose-2 results | 44
Fig. 5.1 Left→ First test with anchor, Right→ Second test within geofence | 47
Fig. A-1.1 I2C bit structure | 54
Fig. A-1.2 Simple serial structure | 54
Fig. A-1.3 UART frame | 54
Fig. A-1.4 SPI structure | 55
Fig. A-1.5 USB master-slave and tiers | 55
Fig. A-1.6 Types of USBs and cable structure | 56
Fig. A-1.7 NRZI-S coding | 56
Fig. A-1.8 USB 2.0 transmission frames | 57
Fig. A-1.9 CAN transmission | 57
Fig. A-1.10 CAN frame | 58
Fig. A-1.11 Simple LDO (Linear Drop-Out) Regulator | 59
Fig. A-1.11 Very Basic Buck Converter (Switching regulator) | 59
Fig. A-1.12 Left → ESC with 2 LDO and a small MCU, Right → Small BEC circuit | 60
Fig. A-1.13 Left→ Capacitor rectification to drops, Right→ AC filtering from DC source . . 60
Fig. A-1.14 Types of capacitors | 61
Fig. A-1.15 Left→ Ferrite around a cable, Right → PCB ferrite beads | 61
Fig. A-1.16 Left→ π-type, Right → T-type | 62
Fig. A-1.17 Schottky Diode | 62
Fig. A-1.18 TVS (Transient Voltage Suppression) Diodes | 63
Fig. A-1.19 Schematic of how Flyback diode works | 63
Fig. A-1.20 Zener Diode | 63
Fig. A-1.21 Basic schematic of a diode bridge | 64
Fig. A-1.22 ST-Link V2 SWD | 65
Fig. A-1.23 Symbol crystal oscillator, electrical model and real examples | 65
Fig. A-1.24 Left→ Example of an oscillator IC, Right→ Example of TCXO | 66
Fig. A-1.25 PCIe Modular GPSDOs with atomic clock | 67
Fig. A-1.26 Acci FPV Flight Controller | 69

Fig. A-1.27 STM32F405 connections | 70
Fig. A-1.28 Oscillator, decoupling and boot connections | 70
Fig. A-1.29 MPU 6000, BMP 280 and ESC connector | 71
Fig. A-1.31 I2C bus, USB, UART/SWD, SBUS and radio | 71
Fig. A-1.32 Reverse polarity protection and BEC at 5V | 72
Fig. A-1.33 BEC at 10V, VBUS-3V3 regulator and VBAT detection | 72
Fig. A-1.34 Flash memory and OSD | 72
Fig. A-1.35 PULPY FC F405 | 73
Fig. A-1.36 PULPY STM32F405RGT6 | 73
Fig. A-1.37 Oscillator and a battery voltage detector | 74
Fig. A-1.38 Magnetometer (ST8310), Barometer (DPS368XTS) and IMU (ICM-42688) . . . 74
Fig. A-1.39 I2C, UART and SWD | 74
Fig. A-1.40 USB bus and conditioning | 75
Fig. A-1.41 Battery Buck converter and linear converter from 5V to 3V3 | 75
Fig. A-1.42 FLASH SPI and RGB string chip | 75
Fig. A-1.43 NxtPX4v2 | 76
Fig. A-1.44 STM32H743VIH6 | 76
Fig. A-1.45 IMU BMI088 and Barometer SPL06 | 77
Fig. A-1.46 USB-C connector and SBUS converter | 77
Fig. A-1.47 Main voltage filter | 78
Fig. A-1.48 9-10V Regulator, 4-5V Regulator and 3V3 Regulator | 78
Fig. A-1.49 FRAM for MCU and MicroSD connector | 78
Fig. A-1.50 FC F4BY H743 | 79
Fig. A-1.51 STM32H743VIT6 | 79
Fig. A-1.52 IMU, Barometer and Compass | 80
Fig. A-1.53 USB-C, PWM-Servo, Camera and CAN bus connectors | 80
Fig. A-1.54 Main voltage regulator circuit | 80
Fig. A-1.55 SD-Card connection and FRAM | 81
Fig. A-2.1 Mars atmosphere diagram | 83
Fig. A-2.2 Venus atmosphere diagram | 84
Fig. A-2.3 Titan atmosphere diagram | 84
Fig. A-2.4 IPC standard tree | 86
Fig. A-2.5 IPC-2221 standard tree | 87
Fig. A-2.6 Via and delamination | 87
Fig. A-2.7 Via plating and positive etch back treatment | 88
Fig. A-2.8 Dendrite grow | 89
Fig. A-2.9 Via-Pad errors and solder reflow steps | 89

Fig. A-2.10 (A) bent leads, (B) deformed leads, (C) damaged leads | 90
Fig. A-2.11 FOD in PnP process | 90
Fig. A-2.12 Tin Whiskers short circuit | 91
Fig. A-2.13 Coating thickness | 92
Fig. A-2.14 NASA MIL-PRF-38535M revision | 94
Fig. A-2.15 RHA levels | 95
Fig. A-2.16 Component designator in MIL-PRF-38535M | 95
Fig. A-2.17 Test temperatures | 96
Fig. A-2.18 Flow diagram for ionizing radiation test procedure | 97
Fig. A-2.19 Paschen curves for different gases, from Dunbar, 1988 | 98
Fig. A-2.20 Example of automated fine pitch routing and possible improvements | 101
Fig. A-2.21 Single event effects | 104
Fig. A-2.22 LET at the microscope | 105
Fig. A-3.1 Board case | 108
Fig. A-3.2 3D printed case components | 108
Fig. A-3.3 Motor PWM connector order | 109
Fig. A-3.4 Mounted drone with designed flight controller and connections | 110
Fig. A-3.5 Left→First test; Right→ Example of autonomous mission | 110

## List of tables

## INTRODUCTION

Since the appearance of the first unmanned vehicle in 1849 in the form of a balloon and its formal introduction in conflicts between 1917-1942, drones have changed the paradigm of interacting with the environment indirectly.

During this early start of the XXI century, drones have taken a very important role in society in multiple aspects. Such as the transport of goods, reconnaissance activities, mapping, firefighting and more. The development of IoT and cheap electronics impulses and leads drones into a promising insight of a better future.

Motivation and objectives

This TFM is devoted to learning, exploring and expanding knowledge of the basic components essential for creating autonomous devices.

Control and power distribution boards are critical subsystems in unmanned vehicles. This project focuses on the complete design process of a dedicated drone control PCB. Furthermore, it includes a study of potential space applications and their specific technical requirements.

The principal objectives of this TFM are:

1. Develop a functional drone control PCB.
2. Create the drivers to manage the drone control PCB with ArduPilot.
3. Evaluate the current design and expose space requirements.

Structure

The project is composed of 5 chapters and 3 annexes:

- Chapters:
- Chapter 1 and 2: Hardware design and routing of a flight controller.
- Chapter 3: ArduPilot software porting into designed hardware.
- Chapter 4: Space applications and hardware analysis.
- Chapter 5: Tests, issues, cost, environmental and social impact.
- Conclusions.
- Annexes:
- Annex-1: Basic PCB analysis of flight controller components and several market flight controllers.
- Annex-2: Space environment and electronics space standards overview.
- Annex-3: Testing, project issues, comparison and cost.

## CHAPTER 1. PCB SCHEMATIC DESIGN

This chapter details the design of the PCB schematics. It begins with an introduction to the requirements and applicable standards, followed by a brief explanation of the composition of each system, balancing reliability, cost and performance.

### 1.1. Introduction to the basics of the architecture of a flight

controller

The flight controller acts as the brain of the aircraft, executing a continuous feedback loop to maintain stability and follow pilot commands. The MCU (Microcontroller Unit) serves as the central processor, managing real-time data from an IMU (Inertial Measurement Unit), which typically combines an accelerometer and a gyroscope, to determine the drone's attitude. To ensure precise flight, the architecture includes barometers for altitude hold and various voltage regulators to provide clean, stable power to sensitive electronics. Furthermore, the flight controller can integrate storage units and specialized communication buses such as UART, CAN, SPI and I2C, to interact with external peripherals like GPS, ESCs, and receivers. This forms a cohesive ecosystem that acquires data, computes control corrections, and generates precise actuator commands to achieve physical movement.

Referencing ANNEX-1 is highly recommended to understand the electronic components used in current hobbyist and commercial drone control boards, as well as their specific manufacturing requirements.

### 1.2. Pixhawk Standards and Software

### 1.2.1. Pixhawk Standards

There is a wide variety of drone controller boards and systems on the market. While the vast majority do not follow any specific standards, professional grade controllers typically follow established conventions.

One of the most famous standards for professional open source controllers is the Pixhawk standards [1]. In fact, Pixhawk is known by the flight controllers open-source family based on Pixhawk Standard. These flight controllers can be programmed with PX4 and ArduPilot operating firmwares.

Regarding Pixhawk Standards, there are many varieties, but these are divided into:
- Pixhawk Autopilot Reference Standards:
- Autopilot v6x Standard (FMUv6): Describes the hardware architecture requirements. FMU stands for Flight Management Unit.
- Autopilot v5x Standard (FMUv5)
- Autopilot v6C Standard (FMUv6)
- Autopilot v6U Standard (FMUv6)
- Autopilot Bus Standard: Addresses bus protection and configuration, specifically between PCBs and peripherals.

- Autopilot Connector Standard: Defines the hardware and pin selection required to provide connections, mainly to peripherals.
- Pixhawk Payload Bus Standards:
- This standard covers design considerations, as well as software and hardware interfaces for cameras, gimbals, actuators and general payloads.
- Pixhawk Smart Battery Standard (Coming soon)

Standard autopilot architectures typically use a main processor for computation and a coprocessor for I/O, sometimes involving up to three processor units. This type of configuration is too complex for the current project. Therefore, the developed PCB uses a single high performance processor, following the Autopilot Connector-Bus Standard.

### 1.2.2. Software

Drone firmware can be present in multiple forms. Generally most flight controllers can be programmed with open source firmwares, with common C language, Arduino or HAL (Hardware Abstraction Layer). Some developers even choose to program unmanned vehicles on bare metal, which is possible but difficult.

Some open-source firmwares are:

- ArduPilot: Professional grade firmware, accurate and robust. Its main GCS (Ground Control Station) is Mission Planner. [2]
- PX4: Devoted for investigation (ROS, Robot Operating System) and autonomous operations; created by Pixhawk. It uses QGroundControl. [3]
- Betaflight: Devoted to FPV drones. Basic firmware that works well on small boards. The same Betaflight provides the GCS. [4]
- INAV: In the middle path between ArduPilot and Betaflight. Used on FPV with positioning systems that seek more precision than Betaflight. [5]

Before creating a controller board, firmware has to be selected beforehand. Programs like Betaflight work with most standard sensors and MCUs (Microcontroller Units). However, ArduPilot and PX4 generally expect specific buses and components.

This does not mean you can't use different chips, but using supported hardware makes programming the bootloader much easier. Advanced users can modify the source code to support any MCU or sensor, but this is complex and not recommended for beginners.

In this project as it tries to develop a professional grade board, ArduPilot was chosen.

### 1.3. PCB Schematics

The PCB design was carried out using Altium Designer. All the schematics, footprints and steps files were obtained from Altium itself [6], EasyEDA [7], UltraLibrarian [8] and Component Search Engine [9], (SamacSystem in other words). To mention that not always all the footprints, schematics are the identical between these sources; some of them can contain errors, so a previous datasheet and manufacturer capabilities search has to be done before manufacturing.

The chosen manufacturer was JLCPCB, due to its capabilities, material selection, market status and cost, [10].

Since the hardware is designed with the intention of being ported to ArduPilot, strict adherence to ArduPilot's data and library requirements was mandatory. Otherwise, some buses or components may not work correctly or might need special drivers. If the reader wants to know more about this, please take a look at the Porting chapter of this TFM.

### 1.3.1. MCU system

The principal component of a drone controller is the MCU (Microcontroller Unit). Since the objective of this project is to produce a professional-grade system, the STM32 family was selected as the optimal architecture. Some typical MCUs used on drones and available to use with ArduPilot are:

- STM32F405: One of the most common MCUs for drones, only one core ARM Cortex-M4, max frequency of 168 MHz, 1 MB Flash, 192 KB RAM, FPU (Single-precision of 32 bits), and the ART Accelerator (which functions similarly to a cache). Its cost is around 3-8 €. Found on boards around <100 €.
- STM32H743: Commonly found in some high end drones, only one core ARM Cortex-M7, max frequency of 480 MHz, 2 MB Flash, 1 MB RAM, FPU (Double-precision of 64 bits) and with cache L1. Its cost is around 6-15 €. Found on boards around 70-400 €. [11], [12]
- STM32H757: Not so common in drones, however Pixhawk and high end controllers like Pixhawk Cube Orange+ use this MCU in parallel with another MCU, do not confuse it with Standard Cube Orange that uses a version similar to the H743 processor. H757 uses dual core (ARM Cortex-M7 + ARM Cortex-M4), it can achieve frequencies of M7-480 MHz and M4-240 MHz, 2 MB Flash, 1 MB RAM, FPU (Double and Single precision), and cache L1. Its cost is around 15-25 €. Found on boards around +450 €.

ArduPilot struggles with 1 MB of storage, as the firmware is almost 1 MB. This is because it contains multiple lines of code and complex drivers such as the use of DMA (Direct Memory Access).

This project uses the STM32H743 as it is a good MCU with enough Flash. Another option is to provide external memory but it is better to keep things simple. Specifically the package LQFP100 (100 pins) in STM32H743VIT6 version, with the silicon revision V. It is a small package, ideal for small applications, and it can work within a wide range of temperatures.

### 1.3.1.1. Conditioning

This section outlines the essential conditioning and support circuitry for the MCU. This processor is powered by 3.3 V with a max current of 620 mA. The maximum voltage admitted by the MCU is around 4 V, although specific pins are 5 V tolerant. All ceramic capacitors must have a maximum tolerance of 20% and be placed as close as possible to the MCU pins. These MCU power pins require a specific conditioning:

- VDD and VDDA pins: The VDD power line requires a 100 nF decoupling capacitor at each pin, plus a single bulk 4.7 µF capacitor. Similarly, VDDA and VREF require 100 nF per pin and a 1 µF bulk capacitor.
- VBAT and VCAP pins: VCAP only needs a 2.2 µF capacitor connection with less than 100 mΩ of ESR (Equivalent Series Resistor). While VBAT has to be connected directly to the power supply though a 100 nF capacitor can be useful to apply for stability.
- NRST pin: Pin used to reset the MCU, external pull up 10 kΩ resistor often used in design though not necessary.

Fig. 1.1 NRST generic scheme

- BOOT pin: Used to place the MCU into bootloader mode, enabling programming via interfaces such as USB or UART. By default, it requires a 10 kΩ pull-down resistor. To activate bootloader mode, the pin is pulled to 3.3 V (typically via a resistor or jumper). A 100 nF capacitor is added for noise reduction.

The ESD (ElectroStatic Discharge) voltage protection of the pins using HBM (Human Body Model) is around 1 kV while the CDM (Charge Device Model) is around 250 V.

External protection to data lines has been added with TVS diodes, specifically TPD2E2U06DRLR (+25 kV) IC; with a breakdown of 6.5 V, not close to the operating voltage but with a low capacitance of 1.5 pF, ideal for high speed data transmission.

### 1.3.1.2. Clocks

The internal clock for these processors is a charged switched capacitor, which is not ideal. 2 External clocks are needed. ArduPilot admits these clocks in direct or bypass mode. The applied option has been bypass mode for both clocks: HSE (High Speed External oscillator) and LSE (Low Speed External oscillator or known as the real clock).
- HSE: The MCU supports an external input frequency range of 4-50 MHz. The chosen HSE has been SIT1602AI-22-33E-26MHz [13]. This IC is a MEMS (Micro ElectroMechanical System) without quartz, it vibrates with a special silicon structure. It is more reliable for systems like drones as it is more resistant to vibrations and impacts. Its stability is around 25 ppm. Only a 100 nF decoupling capacitor and a <10 kΩ pull up resistors are required for the conditioning of this circuit.

During the development of this board, due to software compatibility issues with ArduPilot this initial chip was substituted by ASEMB-24.000MHZ-LC-T [14]. The difference between them is minimal, but this new clock runs at 24 MHz instead of 26 MHz, making it ArduPilot compliant. However, it has a lower precision of 50 ppm.

Fig. 1.2 Clock generic scheme

- LSE: Named as RTC (Real Time Clock), the MCU standard frequency is 32.768 kHz, the SIT1552AI-JE-DCC-32.768D was chosen [15]. This programmable IC is extremely small, smaller than a grain of rice and provides precise timing with a deviation of only 5 ppm. Furthermore, it is considered the world's smallest TCXO (Temperature Compensated Crystal Oscillator). No external conditioning circuitry was required.

Fig. 1.3 LSE scheme

### 1.3.1.3. Pins and Schematics

The pin assignment and configuration were performed using STM32CubeIDE [16]. This environment allows for the selection and distribution of communication buses and peripherals according to the project's specific requirements.

Pins devoted to interruptions have been configured as EXTI (External Interruptor), while for normal I/O pins, only generic GPIO (General Purpose Input/Output) are used. In total, 80 out of 100 pins are used.

Fig. 1.4 Pin selection with STM32cubeIDE


Fig. 1.5 MCU schematics


Fig. 1.6 Decoupling capacitor scheme

### 1.3.2. IMUs: ICM20602 and BMI088

Professional boards often carry multiple IMUs (Inertial Measurement Units). Some of them use the same type of IMU, though having different ones can provide greater reliability. As this board has to be compatible with ArduPilot, both IMUs must be compatible as well. Both sensor ICs are 6-axis, with a gyroscope and an accelerometer.

- ICM-20602:
This is a 6-axis motion tracking device with an LGA package, created by InvenSense. Its maximum operating voltage is up to 3.45 V, sufficient for the power source of the board, which is 3.3 V. The connection with the MCU is via a high-speed SPI bus. This is due to the need to obtain rapid and reliable real-time data regarding the drone's movement, as required by ArduPilot. TVS diodes and decoupling capacitors have been applied.


Fig. 1.7 ICM-20602 and datasheet scheme [17]

- BMI088:
This is a common 6-axis motion tracking device with an LGA package, created by Bosch. The operating voltage of this sensor is similar to the MCU. The connection with this IC is via high-speed SPI, on a completely different bus with respect to the ICM-20602. This is done for reliability. Additional interrupts for this IC are not used; only the minimal pins are connected. TVS diodes and decoupling capacitors have been used.

Fig. 1.8 BMI088 and datasheet scheme [18]

### 1.3.3. Barometer and Magnetometer: BMP388, BMM150

Both sensors are connected using the same I2C bus. The magnetometer and barometer are not critical components for basic stabilization, so I2C is ideal as it is a moderate speed bus. The pull-up resistors used are 2.2 kΩ, enabling communication frequencies of 100-400 kHz. Both Bosch sensors can accept up to 3.6 V, and they are ArduPilot compliant with different addresses. Furthermore, like the previous sensors, they are equipped with interrupt pins. Decoupling capacitors have been placed near the ICs.


Fig. 1.9 BMP388, datasheet and used schematic [19]


Fig. 1.10 BMM150, datasheet and used schematic [20]

### 1.3.4. Differential Buses: CAN and USB-C

- CAN (Controlled Area Network) bus:
Common or non-professional control boards rarely carry this kind of bus. CAN bus is a highly reliable bus. The typical transceivers for this CAN as Pixhawk Standard describes are: TJA1051TK3/118 or LTC2875 (implementing the ISO 11898-2:2016). The used one is the TJA1051TK/3/IJ [21], which goes at 4.5-5.5 V. This model allows sending data at a lower voltage to the MCU using an IO power pin, up to 3.3 V.

In addition Pixhawk Standard provides the order of the cables with the typical SM04B-GHS JST connector:

Table 1.1: CAN

Pin | Signal | Voltage
1 (red) | VCC | +5 V
2 (blk) | CAN H | CAN High
3 (blk) | CAN L | CAN Low
4 (blk) | GND | GND

Additionally a 120 Ω termination resistor is needed. Twist cables are recommended on the peripheral side to reduce EMI (Electromagnetic Interference) to ensure the same area of interference between cables, and reduce the same one. Additionally, decoupling capacitors have been applied as the datasheet schematic mentions.

Fig. 1.11 CAN, datasheet and used schematic

- USB bus:
This bus is dedicated to a direct connection between the personal computer and the MCU. To function as a termination device, the USB standard requires 5.1 kΩ resistors on the CC pins.

Most drone controllers can power the PCB at 5 V from the USB; however, this PCB does not allow that. It only detects if the USB is connected. This is because the power consumption of the PCB and all peripherals can be higher than 0.5 A. While often this setup would be fine, if the user plugs a high consumption peripheral, a higher current could be triggered. If the user's computer cannot handle that, it becomes a problem.
The USB 2.0 standard limits the maximum current to 0.5 A. Despite this, for safety and preventive reasons, there is no direct power connection between the USB VBUS and the board's supply.

Additionally filtering and TVS protection for 5 V detection is provided.


Fig. 1.12 USB-C 2.0 FS schematic

### 1.3.5. Debug and Peripheral Buses

All ports are within the Pixhawk standard using JST connectors.

- Debug SWD:
This bus is the most important one, it allows direct programming between the user’s debugger and the STM32. There are 2 Pixhawk standards;

nevertheless, none of them was applied. A custom connector has been used, composed of: 3.3 V as a power line, SWDIO to program the MCU, SWCLK as a clock line, NRST to reset the MCU and additionally a SWO optional line devoted to printing debug commands.


Fig. 1.13 Debug connector

- SPI:
The SPI bus connector follows the Pixhawk standard. A clarification regarding signal naming is necessary; the industry is transitioning from terms like MISO (Master Input Slave Output) to the modern CIPO (Controller In Peripheral Out).

When wiring, this line must be connected to the peripheral's MISO or SDO (Serial Data Output). Confusion appears when components like sensors use SDI/SDO labeling. In these cases, the connection follows the data flow: the MCU's MOSI (acting as SDO) must be connected to the peripheral's SDI (Serial Data Input). The previous convention was more simple, direct connection MOSI to MOSI and MISO to MISO.

Table 1.2: SPI

Pin | Signal | Voltage
1 (red) | VCC | +5 V
2 (blk) | SCK | +3.3 V
3 (blk) | MISO | +3.3 V
4 (blk) | MOSI | +3.3 V
5 (blk) | SS1 | +3.3 V
6 (blk) | SS2 | +3.3 V
7 (blk) | GND | GND

Fig. 1.14 SPI connector

- I2C:
The design mostly has followed the Pixhawk standards except for the resistor value. The pull up resistor used is 2.2 kΩ, which handles more or less the same bus speed without having any issues.

Table 1.3: I2C

Pin | Signal | Voltage
1 (red) | VCC | +5 V
2 (blk) | I2C SCL (1.5 kΩ recommended) | +3.3 V
3 (blk) | I2C SDA (1.5 kΩ recommended) | +3.3 V
4 (blk) | GND | GND

Fig. 1.15 I2C connector
- Telemetry:
Similar to Pixhawk standards, optional dedicated hardware flow control pins are not used (RTS = Request To Send and CTS = Clear To Send). On the peripheral side, TX/RX must be crossed; this means the TX line at the MCU has to be connected to the RX line of the peripheral.

Table 1.4: Telem

Pin | Signal | Voltage
1 (red) | VCC | +5 V
2 (blk) | TX (out MCU) | +3.3 V
3 (blk) | RX (in MCU) | +3.3 V
4 (blk) | CTS (in MCU) (optional) | +3.3 V
5 (blk) | RTS (out MCU) (optional) | +3.3 V
6 (blk) | GND | GND

Fig. 1.16 Telemetry connector

- Basic GPS:
The Pixhawk standard provides multiple versions for the GPS port. The full GPS mode contains pins for a buzzer, LED and safety switch. However, this configuration is only present in a small group of devices, so it has been discarded. Only the Basic GPS connector has been applied.

Table 1.5: GPS

Pin | Signal | Voltage
1 (red) | VCC | +5 V
2 (blk) | TX (out MCU) | +3.3 V
3 (blk) | RX (in MCU) | +3.3 V
4 (blk) | External I2C SCL | +3.3 V
5 (blk) | External I2C SDA | +3.3 V
6 (blk) | GND | GND

Fig. 1.17 GPS connector

- 2.54 mm Pins:
To provide motor and servo outputs, 8 typical 2.54 mm connector pins are used. These 8 PWM outputs come from 3 different MCU timers (Timers 2, 3, and 4). Moreover, the outputs can provide not only PWM signals but also other standards.

Regarding the connection of SBUS and RCIN, 2 pins are available to receive signals via a UART-RX. A direct connection is usually complex because SBUS is an inverted logic signal. An external inverter IC would be needed in case of using an ARM Cortex-M4 (like the STM32F405) due to the lack of inversion on its UART. Despite this, the STM32H7 provides internal signal inversion within the IC package.

Fig. 1.18 2.54 mm connectors

### 1.3.6. Direct Power and Battery 5V

This PCB has been designed to be powered by 3 means: connecting a Pixhawk Power cable, connecting with a 2.54 mm pins UBEC cable or connecting directly to the battery.

- Pixhawk Power Connector:
This method uses the power connection of the Pixhawk standard; the lines should provide at least 2.5 A. It is important to mention that this connection provides two analog measurements: current and voltage from the battery.

These measurements were initially filtered with an RC filter, but it is crucial to understand the real source of these values. If they come from an amplifier, an RC filter works well. However, if they come from other means, such as a shunt resistor or voltage divider, the filter's resistor affects the final measurement. After testing the board, only a filtering capacitor is required, as the system measures values directly from a voltage divider and shunt resistor, sending the signal to the MCU ADCs.

Table 1.6: Power connector

Pin | Signal | Voltage
1 (red) | VCC | +5.3 V
2 (blk) | VCC | +5.3 V
3 (blk) | Current (analog) | +3.3 V
4 (blk) | Voltage (analog) | +3.3 V
5 (blk) | GND | GND
6 (blk) | GND | GND


Fig. 1.19 Power Pixhawk connector

- Battery Connection:
This circuit has been designed to connect the battery directly to the board or by connecting an UBEC cable. The main component of this circuit is a buck converter. This was designed using Webench with an input of 6-36 V (nominal of 4S-6S) and an output of 5.5 V with a maximum current of 3 A.

The frequency used is 504 kHz with an efficiency of +90%. Regarding the capacitors, their ESR (Equivalent Series Resistance) values are close to the ideal, although actual component characteristics vary slightly.


Fig. 1.20 Converter efficiency and circuit 6-36 V to 5 V [22]

Additionally a reverse protection circuit and a 3 A fuse have been applied at the input. This reverse protection circuit is composed of a P-MOSFET of 100 V, a 100 kΩ resistor and a 12 V Zener diode. While the MOSFET's orientation provides the reverse polarity protection, the Zener diode and resistor are critical for gate-source voltage clamping. Since the input voltage can reach 36 V (nominal 6S), applying this potential directly to the gate would exceed the MOSFET's maximum rating (following the datasheet a maximum of -20 V), leading to dielectric breakdown. The Zener diode limits the voltage drop across the gate to a safe -12 V, while the resistor limits the current through the Zener, ensuring the MOSFET operates safely within its specifications regardless of the high input voltage.

At the output of the converter, the design includes a TVS protector against voltage increment, a Schottky diode to protect against reverse current, and a 2.54 mm header to connect with a UBEC cable. The Schottky diode will reduce the output voltage from 5.5 V to around 5.1 V. Furthermore, it is important to use an external polymer capacitor at the battery connector to protect against noise (470 µF with low ESR).

Moreover, a simple voltage divider was designed to detect battery presence and voltage level; however, due to ArduPilot mapping constraints, this voltage measurement on microcontroller ADC-3 was not possible to implement.


Fig. 1.21 Overall circuit diagram 6-36 V to 5 V

### 1.3.7. Power 3.3 V

This circuit powers the entire board, with the exception of the external peripherals and the CAN transceiver. Two identical, independent circuits have been designed (one for peripherals and the second for the board).

These converters, developed with Webench, accept an input of 3.8 V to 6 V and provide an output of 3.3 V with a maximum current of 2 A. The maximum estimated current draw is below 1.25 A. This simple buck converter operates at 1.39 MHz and achieves an efficiency of +90%. As it is a high-frequency converter, 100 nF ceramic capacitors are ideal to filter noise near the sensors and the MCU.

Fig. 1.22 Converter efficiency and circuit 5 V to 3V3 [23]


Fig. 1.23 Overall circuit diagram 5 V to 3V3

### 1.3.8. Storage: MicroSD

Drone boards commonly store data within Flash or RAM. While internal RAM is sufficient for the MCU's operation, external Flash storage is essential if the user wants to record flight logs.

The vast majority of microcontrollers save this data using the SPI bus. However, high-end drones avoid this due to speed limitations and DMA sharing constraints (Direct Memory Access). Better methods can be applied, such as SDMMC (Secure Digital and MultiMediaCard). This bus can transfer between 24-48 MB/s, depending on the card used. There are multiple modes; the chosen one is the 4-bit mode, which allows fast storage (storing 4 bits per clock cycle), using CMD for commands and CLK as the clock.

To create this circuit, trace length matching is necessary between lines. Additionally, pull-up resistors are required on all lines except the clock.


Fig. 1.24 Overall circuit diagram MicroSD

### 1.4. Other considerations

All resistors and capacitors selected for the design are 0402 size or larger to minimize assembly costs and potential defects.

Moreover, wherever feasible, component standardization was prioritized. Using the same component type across multiple systems such as choosing a single standard value for capacitors or resistors significantly reduces production costs by simplifying the BOM (Bill of Materials).

Component availability was also key. Manufacturers' available quantity and lifetime cycle has to be considered, as well as potential alternatives.

Additionally, the design includes dedicated test points on important power and signal lines. For instance: un-tented vias (exposed vias) can be used as points for signal probing.

## CHAPTER 2. PCB ROUTING DESIGN

This chapter provides a simple explanation of the PCB routing strategy. It begins by addressing the layer stackup and impedance constraints, followed by the routing process and concludes with the files required for manufacturing and assembly.

### 2.1. Manufacturing Capabilities and Layer Stackup

Manufacturing has been one of the most challenging parts of this project. The 2 biggest constraints were tolerance requirements and material availability. To produce the board, the chosen manufacturer was JLCPCB. This explanation focuses only on rigid PCBs.

### 2.1.1. Capabilities

The capabilities of the PCB manufacturer have a decisive role in the design process, defining the limits for DFM (Design for Manufacturability) and PCB Assembly (PCBA) feasibility. The board was designed in compliance with the manufacturer's constraints. The key manufacturing capabilities and design rules are summarized below [24]:

1. Stackup and materials:
- Number of layers: up to 32 layers.
- Core material: FR-4, Al, Co, Rogers or PTFE (Polytetrafluoroethylene).
- Core dielectric constant: usually 4.5 for FR-4.
- Maximum PCB dimensions 670x600 mm and tolerance 0.1 mm.
- Thickness: 0.4-4.5 mm.
- Surface finish: HASL, ENIG or OSP.
2. Routing and copper:
- Impedance tolerance: 10%.
- Copper layer weight: 0.5 oz, 1 oz, 2 oz, etc.
- Track width and spacing (3.5/3.5 mil) (this depends on copper weight).
- Track tolerance: 20%.
- SMD pad to pad clearance: 0.15 mm.
- BGA pad diameter: 0.25 mm.
- Copper distance clearance: 0.2 mm.
- Pad to track clearance: 0.1 mm.
3. Drilling and vias:
- Hole size: 0.15-6.3 mm (5.9-248 mil).
- Blind/buried vias.
- Plated and non-plated slots or holes.
- Via-to-via spacing: 0.45 mm.
- Via to hole clearance: 0.2 mm.
- Min NPTH/PTH annular ring distance: 0.45/0.2 mm.
4. Soldermask and silkscreen:
- Soldebridge: 0.1 mm.
- Soldemask expansion: 1:1.
- Soldemask dielectric constant: 3.8.

- Silkscreen width and clearance: 6 mil/0.15 mm.
- Panelization, and many more.

### 2.1.2. Layer Stackup

The layer stackup comprises the main board materials and is critical because it defines aspects such as signal integrity, EMI (Electromagnetic Interference) behavior, power integrity, cost and reliability.

The main objective of this project is to develop a flight controller prototype, making cost a relevant factor. To reduce expenses, a standard controlled impedance stackup has been chosen. While this is not a high-density drone stackup (which typically consists of 6-10 layers), it is more robust and feasible for repairs. This approach provides a balance between professional performance and prototyping flexibility.

Table 2.1: Layer stackup

This 1.6 mm stackup is a base standard in JLCPCB [25], composed of an FR-4 core and Prepreg 7628 (glass fiber with semi-cured epoxy and a dielectric constant of 4.4). Copper layers range from 0.5 oz for inner layers and 1 oz for outer layers.

It is important to mention that the stackup selection depends on trace impedance, connection complexity and environment. To reduce manufacturing costs, all vias are through-hole; this means every vertical connection crosses all four copper layers.

Regarding the layout, having a symmetric stackup is crucial to reduce thermal stress in the Z-axis and prevent warping. The designed drone PCB uses L1 and L4 as the primary signal layers, while L2 is dedicated to grounding (as a reference plane) and L3 is used for grounding and power distribution.

### 2.2. Trace Impedance Calculation

Trace impedance and reference grounding is quite important for signal transmission.

The trace characteristic impedance can be defined as:

Z | or | (2.1)
0 =

R+jwL
G+jwC

Z
approx

≈

L
C

Where L and C stands for inductance and capacitance while R and G stands for resistance and conductance. When designing a track:

- If the track increases width, the surface area increases. This causes higher capacitance (more charge can be stored) and lower inductance. The result is a lower characteristic impedance.
- If the distance between the reference plane and the signal track increases, capacitance decreases and inductance increases. The result is a higher characteristic impedance.
- If the dielectric constant of the material is higher, capacitance increases. The result is a lower characteristic impedance.

In the design of a PCB, the most used formulas are from IPC-2141 standard, though these can contain an error of 7%. The symbol ε stands for material relative
r
permittivity or dielectric constant. It measures how much electrical energy can contain the material. For instance: 1 for vacuum and 4.5 for FR-4.

Fig. 2.1 IPC-2141 standard formulas (7% tolerance) (good for 50 Ω) [26]

Another set of formulas commonly used are the Wadell’s impedance equations, these are much more accurate around 1%.

There are multiple online models and calculators available, from simple to complex ones. However, most of them do not take into account dielectric losses (the imaginary part of the dielectric constant), copper losses (skin effect and surface roughness), radiation losses, high-frequency dispersion, or fiber weave effects (statistical non-uniformity of the PCB glass fiber).

Another important aspect is via impedance and specially differential impedance. Differential pairs transmit signals with opposite polarities. Their close proximity ensures tight electromagnetic coupling, making transmission more reliable. If external noise affects one signal, it affects the other in the same way, allowing the noise to be cancelled out. As well as a single track, a differential track can be coplanar or non-coplanar (surrounded by a ground plane). The differential impedance formula from the physical point of view can be defined like:

Z | (2.2) diff = 2Z
odd = 2

L

trace+Lmutual

C

trace+2C
mutual
If we increase the spacing between lines, ↑C | , obtaining a results of | . mutual
Z

diff = 2Z
0
Same result as having a single trace. Despite this formula, the design process does not use this calculus directly as it can become quite difficult to determine these internal values. Instead, design processes use IPC estimation formulas and alternatives, depending on frequency range. An example of these equations is [27], [28], [29]:


Fig. 2.2 IPC-2141 differential formulas for microstrip (5-10% tolerance)

### 2.2.1. Impedances on the PCB

Regarding the designed PCB, three main impedances were calculated. While the target impedance for the main traces is 50 Ω, this was not strictly followed throughout. Since this is not a radio frequency board, trace widths were varied to optimize connectivity and thermal relief.

In order to provide CAN connectivity, CAN bus requires a 120 Ω differential impedance. While USB FS, requires a 90 Ω differential impedance. In parallel with the layer stackup [25], these dimensions were chosen to provide a reliable connection.

Table 2.2: CAN/USB bus differential bus impedance

### 2.3. PCB Routing

Routing a PCB seems an easy task, though it is not. Manufacturer tolerances, number of layers, material used, component design, component spacing and reparation design can cause a lot of problems. There are many topics to expose but I will try to focus on those that are important.

The designed board can be seen in the following pictures.


Fig. 2.3 PCB design (Left→ L1 to L4, Center→L4 to L1, Right→3D STEP)

The board outline and mounting holes (including copper clearance) were designed using AutoCAD and Altium, aiming to reduce size and repair operation. During the design many component footprints were found with errors. Datasheet revision and comparison is required prior position.

### 2.3.1. Power supply design and planes

A 4-layer stack-up was selected for this board design to maximize performance. The use of continuous internal planes provides a solid reference, minimizes crosstalk ( traces do not cross split planes to avoid crosstalk), lowers EMI (Electromagnetic Interference), improves heat distribution and increases current handling capabilities.

- Layer 1 (L1): This is the principal routing layer containing most of the connections. Power converter traces were widened (+60 mil) to safely handle at least 3 A. These are visible at the bottom of the figure below.
- Layer 2 (L2): This is a solid copper GND plane (ground plane), acting as a low-impedance reference for the signals on L1.
- Layer 3 (L3): This is a mixed power/ground plane divided into three zones: an outer ring providing 5 V (powering outer Pixhawk connectors), an intermediate semi-circle distributing 3.3 V to onboard SMD devices (Surface Mount Device) and an inner GND pour to shield L4 and prevent crosstalk.
- Layer 4 (L4): This layer serves as an alternative routing path when L1 is congested, utilizing vias for transitions. By placing all SMD components on the top side and using L4 only for alternative routing, the design is on single-sided assembly, significantly reducing manufacturing costs.

Fig. 2.4 Planes (L1→connections, L2→GND, L3→ reference, L4→ connections)

Standard 0.3 mm hole / 0.6 mm diameter vias were utilized throughout the design to minimize manufacturing costs. These through-hole vias are capable of handling approximately 1.5 A of current. Strategically placed vias are essential for thermal management, current distribution in reference planes and signal routing between layers.

To develop power traces the IPC-2152 standard has been used. This standard is key for manufacturing on power transmission lanes.


Fig. 2.5 IPC-2152 trace table and Nomograph (both related) [30]

The 5 V converter, powered directly by the battery, is shown in the figure below. This converter was designed following the datasheet's recommended layout to provide at least 3 A. It is surrounded by GND planes/thick traces to minimize noise coupling and crosstalk with adjacent circuits. To connect this 5 V power line to the L3 power plane, a group of vias was used. Specifically, 0.3/0.6 mm vias were chosen; larger vias were avoided as they could cause solder bridging, which is not recommended.


Fig. 2.6 5 V Converter (Left→ routing, Center→3D, Right→Datasheet layout)

This board contains two 3.3 V converters that provide an external power source and an internal power source for the board. In terms of design, they are quite similar to the 5 V converter. Therefore, decoupling capacitors should be placed near the output of the converter to ensure signal stability.

Fig. 2.7 3.3 V Converter (Left→ routing, Center→3D, Right→Datasheet layout)

### 2.3.2. Sensor and MCU design

The routing strategy for the sensors and the MCU is quite similar. Decoupling capacitors must be placed in close proximity to these components to minimize noise, ensuring their placement does not obstruct other connections. However, there are specific design constraints to consider:

- Magnetometer: To prevent magnetic interference, no copper pours were placed underneath or near the sensor. The traces are narrow (5 mil), approaching the manufacturer's minimum width limit.
- BMI088 IMU: The two MISO pins, which carry the same output, were merged into a single trace. For very high-frequency applications, this might cause signal integrity issues.
- MCU and Clocks: The STM32 datasheet provided the reference design for connecting the external oscillators (clocks), decoupling capacitors, and power delivery network.


Fig. 2.8 Other connections (Left→ Compass, Center→ MCU+clocks, Right→ BMI088)

### 2.3.3. Connectors and special buses

The Pixhawk power connector serves as an auxiliary power source, supplying 5.3 V to the 5 V power plane while enabling real-time battery monitoring.

A critical interface on the board is the SDMMC bus, which uses parallel data lines operating at high frequencies. To ensure signal synchronization across the 4-bit bus, length tuning was applied.

An accordion pattern was selected for this purpose, although trombone or sawtooth patterns are valid alternatives. A potential drawback of length tuning is the risk of creating crosstalk and acting as an antenna.

Standard practices recommend a spacing of at least three times the trace width (3 W rule) to reduce crosstalk, especially for frequencies above 50 MHz. To reduce antenna radiation, a solid ground reference plane was used. Coplanar tracks, termination resistance and via shielding are recommended to reduce antenna effects. This design could be further optimized by refining the tuning geometry and increasing trace spacing to mitigate noise.


Fig. 2.9 Left→ Pixhawk power connection, Right→ SDMMC bus

The CAN and USB buses are also key components of the design. Both follow the trace width calculated for the required impedance. The USB bus is routed with 2 differential pairs, merging them into a single differential pair with vias within the manufacturer's tolerance limits.


Fig. 2.10 Left→ CAN bus, Right→ USB FS bus

### 2.3.4. Fiducials and possible improvements

Fiducials are a key component of the design. These marks of exposed copper are essential for the machinery that places the components. They must be positioned at the edges of the board, forming a rectangle. Usually, manufacturers require them to be 1 mm in diameter with a 0.5 mm mask clearance/expansion.

Fig. 2.11 Fiducial

The design is not perfect and has potential for improvement. Improvements may include the analog sensing traces and the power distribution network. Specifically, decoupling capacitors should be positioned strictly between the via and the IC pin to force current through the capacitor, rather than connecting the via directly to the pin. Also, the accordion traces require wider spacing to reduce crosstalk.

Fig. 2.12 Left→ Analog measure traces, Center→ Decoupling, Right→ Accordion

90º corners shall be avoided to maintain constant trace width. Sharp corners create impedance discontinuities that can cause signal reflections, potentially degrading the quality of transmissions. Moreover, sharp corners can contribute to EMI (Electromagnetic Interference), abrupt change in geometry concentrates the electric field, which can lead to signal radiation.


Fig. 2.13 Copper corners

### 2.4. Manufacturing files

There are multiple manufacturing files inside the industry. These can be divided into 2 sectors, manufacturing files for boards and manufacturing files for mounting and testing. The files used in this project have been GerberX2, PnP (modified) and BOM (modified).

### 2.4.1. PCB

- Gerber files (i.e: Gerber X2): This is a set of files containing 2D vector representations of the board for each specific layer, including soldermask, pad/via positions, and copper traces. They provide the essential geometric data and guidelines required to execute the manufacturing process.
- OBC++: Similar to Gerber, though its structure is like a database. Owned by Siemens but quite used in the industry nowadays.
- IPC-2581: Modern file format, it provides information from the board manufacturing to even mounting and testing. It is a single file that comprises everything.
- Drilling files: Provides position and size of PTH (Plated Through Hole) and NPTH (Non-Plated Through Hole) drills to the CNC drilling machine.
- Others:
- Board outline
- Fabrication notes, etc.

### 2.4.2. PCBA

- Pick and Place (PnP or CPL): It provides the X-Y coordinates, rotation and layer side of every component to guide the automated assembly machinery. This file has been modified by hand to fulfill the manufacturer's requirements for this project. A total of 146 components. An example would be the following table:

Table 2.3: Example of PnP file

Designator | Comment | Layer | Footprint | Mid X | Mid Y | Rotation | Description
USBR1 | 5.1kΩ | Top | RESC160 8X55N | 94.4880 mm | 87.8840 mm | 90 | Resistor
GPS2 | SM06B-G HS-TB(L F)(SN) | Top | FP-SM06 B-GHS-T B_LF_SN -MFG | 93.5590 mm | 49.1490 mm | 90 | CONN HEADER SMD R/A 6POS 1.25MM

Crucial considerations for manufacturing: It is important to note that the position and rotation of components in the design files must strictly match the manufacturer’s coordinate system; otherwise, the board will be assembled incorrectly. For this project, JLCPCB was used as the manufacturer. Their online viewer allows for component alignment and PCB design verification.

The production files must comply with the manufacturer’s specifications, as manual rotations made within the online viewer will not update the original source files. It is highly recommended to select the "manufacturer file revision" option and manual review when ordering the boards to verify that all components are correctly oriented before production.

- Bill of materials (BOM): A comprehensive list of all components required for the assembly. It maps each reference designator to its specific MPN (Manufacturer Part Number) and package type. This file has been modified by hand to fulfill the manufacturer's requirements for this project. A total of 44 different components. In the example, the final column lists the manufacturer part numbers.

Table 2.4: Example of BOM file

Comment | Description | Designator | Footprint | LibRef | Quantity | LSCS part
BMP388, | P-Sensor SPI I2C 1, 25 Bar SMD | BAR | PQFN50P20 0X200X80-1 0N | BMP388 | 1 | C779278
100nF 1mΩ, | CAP CER 0.1UF 16V X7R 0402 | BMIC1, BMIC2, … | FP-GRM15-MFG | CMP-210 0-03641-2 | 30 | C71629
- Others:
- Solder paste file: File used to create stencil, specific solder paste layer of a Gerber file.
- Assembly drawing: Usually a PDF file containing PCB/PCBA drawing, often used on quality inspection.
- Test and inspection files: There are multiple files to test multiple things. From AOI (Automatic Optical Inspection) to ICT (In-Circuit Test).
- 3D STEP file, etc.

## CHAPTER 3. SOFTWARE PORTING

This chapter provides an overview of how to port ArduPilot firmware to custom STM32 hardware, as well as the required testing to evaluate its firmware functionality.

### 3.1. Creation of files

The board is designed to run ArduPilot software. To install this software, both a bootloader and the firmware must be compiled. A bootloader (sometimes called a bootstrap) is a critical program that acts as a bridge between the hardware and the operating system or main application. It functions similarly to a car's starter motor: it initializes the system before the main software takes control. Common examples in personal computing include BIOS and UEFI.

In the STM32 architecture, the bootloader's role extends to flashing new firmware onto the chip. There are 2 types: the manufactured bootloader (located in a ROM like memory, non-erasable and created by STMicroelectronics) and IAP bootloader (In-Application Programming, custom program placed at the beginning of the flash memory, its job is to handle firmware updates before handing over control to the main program).

Building this firmware requires a specific foundation. ArduPilot runs on top of ChibiOS [31], a system that handles the RTOS and HAL functions necessary for the hardware.

As the process of integrating ChibiOS and creating firmware for custom boards can be complex, I will describe it in a simplified guide covering all the necessary steps. This explanation assumes the use of a Windows computer. Check this for more information: link. (https://ardupilot.org/dev/docs/porting.html)

First of all, to install Linux, open “Powershell" in admin mode. Install wsl:

wsl --install

Reboot the computer after the installation. Once rebooted, install ubuntu with your custom user and password:

wsl --install -d Ubuntu

Then run Ubuntu as admin. It is mandatory to update and install git:

sudo apt update && sudo apt install git -y

To start with ArduPilot, clone the repository. It will appear in the home directory of the Linux environment.

git clone https://github.com/ArduPilot/ardupilot.git

Once with ArduPilot, the best option is to update and check if it is usable. To do so, try these commands:

cd ardupilot
git submodule update --init --recursive Tools/environment_install/install-prereqs-ubuntu.sh -y
. ~/.profile

To test and check an actual commercial grade drone board code:

./waf configure --board MatekH743
./waf copter

If at the end of the command line shows completed or something similar it is possible to build a firmware for a microcontroller.

Knowing that the environment works, the next step is to start creating the custom firmware and bootloader. Open the following folder with commands or manually:

cd ardupilot/libraries/AP_HAL_ChibiOS/hwdef

Inside this directory, it is mandatory to create a new folder, in my case I’ve named “CustomH7”. Add the following files into the folder: the hwdef.dat (firmware file), hwdef-bl.dat (bootloader file) and default.parm (optional file for firmware). The explanation about the creation of these files can be found at the end of this chapter.

To check if they are recognized (hwdef-bl and hwdef mainly):

ls -la

Return to the ArduPilot root directory to build the firmware and the bootloader. The process involves three main steps: building the bootloader, building the firmware and compiling the both. Finally, verify the output files to ensure the build was successful.

cd ~/ardupilot
./Tools/scripts/build_bootloaders.py CustomH7
./waf configure --board CustomH7
./waf copter

In case of troubleshooting with errors, the following commands are to delete previous data created.

./waf distclean
rm -rf build/

All these command lines are devoted to creating arducopter firmware. If the final user only wants to create rover or plane firmwares, it is only necessary to substitute the command:

./waf copter or ./waf copter --board CustomH7
Other possible firmwares to test:
- ./waf plane
- ./waf antennatracker
- ./waf sub
- ./waf blimp
- ./waf rover

### 3.2. Uploading

It is time to upload the bootloader and the firmware inside the board. This can be done in multiple ways, via SWD or DFU. SWD is preferable, it is required to download STM32CubeProgrammer or STM32CubeIDE, though I don't really recommend this last one.

All these programmes can be found in “ardupilot/build/CustomH7/bin/”. Here we can find the 3 main files (bootloader, firmware and bootloader + firmware), these can be in the form of .hex, .bin or .apj. Hexadecimal or binary files are for uploaders/debuggers like the STM32CubeProgrammer [32], while .apj file is used to upload the code in Mission planner.

It is possible to upload firstly the bootloader and then the arducopter firmware,
though | there | are | faster | ways. | To | keep | it | simple, | inside
“ardupilot/build/CustomH7/bin/”, there is a file containing both programs named arducopter_with_bl.hex.

The first step is to open STM32CubeProgrammer and connect the microcontroller via SWD using a debugger (i.e: ST-LINK V3). To ensure a stable connection, it is recommended to set the BOOT0 pin high and perform a power cycle.

Always keep the PCB powered via an external source like a battery. USB power can be unstable and the debugger device often cannot supply current for these boards.

Activating BOOT0 is mandatory to prevent connection failures caused by continuous software resets. This pin forces the board to bypass the Flash and boot from the system memory (manufacturer's internal bootloader).

Upon opening STM32CubeProgrammer, select the interface (typically ST-LINK) and click connect. Once the connection is established, it is recommended to perform a full chip erase to clear previous data. This is done by clicking the button with the eraser icon. These steps can be seen in the following picture.


Fig. 3.1 STM32CubeProgrammer connection and memory delete

After connecting, open the arducopter_with_bl.hex file. Verify that the address is set to 0x08000000 (base address of the Flash memory for STM32H743). Then, click download to flash the data into the MCU. Note: the initial bootloader and firmware address is 0x08000000 while considering only firmware is 0x08020000.

Finally, disconnect the debugger, remove the BOOT0 connection, and perform a power cycle to reboot the board into normal operation.

Fig. 3.2 Uploading steps (in step 2, address should be: 0x08000000)

Right now, the board has all necessary programs loaded. If the user uses a microSD card, ensure it is FAT32 formatted. Without a card, the board might not work properly.

To verify that it works, connect the board via USB (it is recommended to power on/off the device a few cycles, sometimes it does not work at first connection). Open device manager; you should see a new device listed under COM/LPT ports. Open Mission Planner, select the new COM port and connect at a baud rate of 115200. In the message section, errors and information will appear.

### 3.3. Simple firmware testing

To check that the board works well, a minimum of tests shall be applied. The minimum required setup connected to the boards to perform these tests is: a compass or GNSS receiver, a radio receiver and motor or actuator. These are the minimum set of test and their possible solution:

- The board boots correctly and connects to the GCS via USB. If not, check power distribution, clock configuration and hardware design.
- Firmware loads and parameters can be read and written from the GCS. Otherwise check flash configuration and bootloader settings.
- If the HUD shows messages such as “failed to init xyz”, the corresponding peripheral has not been configured correctly in hwdef.dat or in parameters.
- RC input, GNSS receiver and compass are detected and provide valid data. If not, verify hardware, protocol selection and configuration.
- Verify IMU detection and orientation. IMU orientation can be tested by enabling/disabling each IMU using the INSx_USE parameters.
- Check that the board can arm correctly. If arming fails, check hardware and configuration, maybe force it via parameters.
- Verify current and voltage measurements. If values are incorrect, check analog scaling in hwdef.dat and parameters.
- Test motor and servo outputs. If outputs do not respond, check pin assignment, PWM configuration and hardware design.
- Verify that all designed communication interfaces like UART, SPI, I2C, CAN, etc; are functional.
- Other important tests can be: barometer test, failsafe test, logging test (microSD test), reboot and power-cycle tests, DMA test or thermal stability test.

### 3.4. hwdef.dat, hwdef-bl.dat and default.parm

These hwdef.dat and hwdef-bl.dat files are the most important files to port a microcontroller into ArduPilot. These files should not contain any error in typing and in order, because minimal changes won’t allow ChibiOS to create the firmware and the bootloader, or even they won’t work once uploaded inside the MCU, most probably blocking the communication with the SWD bus and with any other available bus.

The hardware and software of the board have to be implemented according to ArduPilot python scripts. These rules explain what components can be used and what functions the microcontroller pins can take, the documentation can be found in the following link. (https://github.com/ArduPilot/ardupilot/tree/master/libraries/AP_HAL_ChibiOS/hwdef/scripts)

Regarding the software files, a good example is the fmuv3. (https://github.com/ArduPilot/ardupilot/tree/master/libraries/AP_HAL_ChibiOS/hwdef/fmuv3)

### 3.4.1. hwdef.dat

This file allows the creation of the firmware. The first step is to define the board nucleus and its memory in KB in binary.

# Core

MCU STM32H7xx STM32H743xx

FLASH_SIZE_KB 2048
FLASH_RESERVE_START_KB 128

Followed by the clock configuration, the system timer and the board information. The clock frequency is 24 MHz, both clocks in bypass configuration. We want a stable system frequency of 400 MHz using the PLL (Phase-Locked Loops) and the general system timer 5. Board information ID/USB_product stands as 1001 for prototyping, USB_Vendor is optional though a random vendor can be used for testing. Lastly, the name of the board and the product.

# Clock

OSCILLATOR_HZ 24000000
STM32_HSE_BYPASS
STM32_LSE_BYPASS
STM32_SYSCLK 400000000
STM32_ST_USE_TIMER 5

# Board names

APJ_BOARD_ID 1001
USB_VENDOR 0x2DAE
USB_PRODUCT 0x1001
USB_STRING_MANUFACTURER "CustomH7" USB_STRING_PRODUCT "FlightController"

Defining the buses pins:

# I2C buses

PB6 I2C1_SCL I2C1
PB7 I2C1_SDA I2C1
PB10 I2C2_SCL I2C2
PB11 I2C2_SDA I2C2

# ICM SPI bus

PA5 SPI1_SCK SPI1
PA6 SPI1_MISO SPI1
PA7 SPI1_MOSI SPI1
PA4 ICM_CS CS

# External SPI bus

PB13 SPI2_SCK SPI2

PB14 SPI2_MISO SPI2
PB15 SPI2_MOSI SPI2
PE8 EXT_CS1 CS
PB12 EXT_CS2 CS

# BMI SPI bus

PE12 SPI4_SCK SPI4
PE13 SPI4_MISO SPI4
PE14 SPI4_MOSI SPI4
PE11 BMI_ACCEL_CS CS
PE10 BMI_GYRO_CS CS

# USB FS bus

PA11 OTG_FS_DM OTG1
PA12 OTG_FS_DP OTG1
PA9 VBUS INPUT

# Sensor data ready pins

PE9 BMI_ACCEL_DRDY INPUT
PE15 BMI_GYRO_DRDY INPUT
PC4 ICM_DRDY INPUT

# Serial pins (NODMA = No DMA) PC6 USART6_TX USART6

PC7 USART6_RX USART6
PD5 USART2_TX USART2
PD6 USART2_RX USART2
PD8 USART3_TX USART3
PD9 USART3_RX USART3
PE0 UART8_RX UART8
PE1 UART8_TX UART8
PE7 UART7_RX UART7 NODMA

# CAN bus pins

PB8 CAN1_RX CAN1
PB9 CAN1_TX CAN1

Definition of buses, battery measurement and motor pins.

# Order of buses: (0, 1, 2, 3, 4, 5, ..)

I2C_ORDER I2C1 I2C2
SERIAL_ORDER OTG1 USART6 USART2 USART3 UART7 UART8

# PWM with GPIO capability (always starting from 50), (TIM=timers) PA0 TIM2_CH1 TIM2 PWM(1) GPIO(50)

PA1 TIM2_CH2 TIM2 PWM(2) GPIO(51)
PA2 TIM2_CH3 TIM2 PWM(3) GPIO(52)
PA3 TIM2_CH4 TIM2 PWM(4) GPIO(53) PB0 TIM3_CH3 TIM3 PWM(5) GPIO(54) PB1 TIM3_CH4 TIM3 PWM(6) GPIO(55) PD12 TIM4_CH1 TIM4 PWM(7) GPIO(56) PD13 TIM4_CH2 TIM4 PWM(8) GPIO(57)

# Battery measurement ADCs with scale factor PC0 BATT_CURRENT_SENS ADC1 SCALE(1) PC1 BATT_VOLTAGE_SENS ADC1 SCALE(1)

# Sensor address and velocity of bus

I2CDEV baro I2C1 0x76 400000
I2CDEV compass I2C1 0x10 400000

# Sensor bus speed definition range, SPI mode and number of connected devices SPIDEV icm20602 SPI1 DEVID1 ICM_CS MODE3 2*MHZ 8*MHZ

SPIDEV bmi088_g SPI4 DEVID1 BMI_GYRO_CS MODE3 8*MHZ 8*MHZ
SPIDEV bmi088_a SPI4 DEVID2 BMI_ACCEL_CS MODE3 8*MHZ 8*MHZ
SPIDEV spi_ext SPI2 DEVID1 EXT_CS1 MODE0 2*MHZ 8*MHZ

Sensor drivers and rotation, MicroSD configuration, storage and DMA priority. True rotation can be verified with Mission Planner by monitoring the HUD (Heads-Up Display) in the Flight Data window, ensuring that the artificial horizon responds correctly to the physical board movements or by using the tuning window.

# Sensor drivers, address and rotation

BARO BMP388 I2C:0:0x76
COMPASS BMM150 I2C:0:0x10 false ROTATION_NONE

#Sensor drivers and rotation

IMU Invensense SPI:icm20602 ROTATION_YAW_90
IMU BMI088 SPI:bmi088_a SPI:bmi088_g ROTATION_PITCH_180

# MicroSD card pins definition and SD mode detection

PC8 SDMMC1_D0 SDMMC1
PC9 SDMMC1_D1 SDMMC1
PC10 SDMMC1_D2 SDMMC1
PC11 SDMMC1_D3 SDMMC1
PC12 SDMMC1_CK SDMMC1
PD2 SDMMC1_CMD SDMMC1
PA8 SD_DETECT INPUT PULLUP

# System PID page storage (usually page 14, away from the main code) and size to store values STORAGE_FLASH_PAGE 14

define HAL_STORAGE_SIZE 32768

# Bus DMA priority (IMU sensors first on the queue)

DMA_PRIORITY SPI1* SPI4* CAN1* SDMMC* USART6*

### 3.4.2. hwdef-bl.dat

This file allows the creation of the bootloader. Really similar to hwdef.dat but much simpler.

# Core

MCU STM32H7xx STM32H743xx

# Clock configuration (frequency and mode) OSCILLATOR_HZ 24000000

STM32_HSE_BYPASS
STM32_LSE_BYPASS

# Board names

APJ_BOARD_ID 1001
USB_VENDOR 0x2DAE

USB_PRODUCT 0x1001
USB_STRING_MANUFACTURER "CustomH7"
USB_STRING_BOOTLOADER "CustomH7 Bootloader"

Regarding the memory it is mandatory to use this strict configuration:

# Mandatory configuration for Bootloader STM32H743

FLASH_SIZE_KB 2048
FLASH_RESERVE_START_KB 0
FLASH_BOOTLOADER_LOAD_KB 128 APP_START_OFFSET 0x20000

# Bus pins

PA11 OTG_FS_DM OTG1
PA12 OTG_FS_DP OTG1
PA9 VBUS INPUT

PC6 USART6_TX USART6
PC7 USART6_RX USART6

# Chip select (often applied in hwdef-bl.dat) PA4 ICM_CS CS

PE11 BMI_ACCEL_CS CS
PE10 BMI_GYRO_CS CS
PE8 EXT_CS1 | CS
PB12 EXT_CS2 | CS

Configuration of bus order and SDMMC. It is mandatory to use the FATFS library to write and read the MicroSD. Moreover SD is enabled to modify and upload firmware.

# Bus serial order of the bootloader

SERIAL_ORDER OTG1 USART6

# Standard configuration drivers for SDMMC (MicroSD) define CH_CFG_USE_MEMCORE 1

define CH_CFG_USE_HEAP 1
define CH_CFG_USE_SEMAPHORES 0
define CH_CFG_USE_MUTEXES 1 define CH_CFG_USE_DYNAMIC 1 define CH_CFG_USE_WAITEXIT 1 define CH_CFG_USE_REGISTRY 1

# SDMMC pins (MicroSD)

PC8 SDMMC1_D0 SDMMC1
PC9 SDMMC1_D1 SDMMC1
PC10 SDMMC1_D2 SDMMC1
PC11 SDMMC1_D3 SDMMC1
PC12 SDMMC1_CK SDMMC1
PD2 SDMMC1_CMD SDMMC1
PA8 SD_DETECT INPUT PULLUP

# Allow the use of FATFS for the MicroSD

define HAL_OS_FATFS_IO 1

# Allow the user to upload the firmware via SD

define AP_BOOTLOADER_FLASH_FROM_SD_ENABLED 1

### 3.4.3. default.parm

This file modifies the parameters inside ArduPilot, they can be changed manually using Mission Planner. That's because it is an optional file.

# Serial 1 (following the order in hwdef, it is UART 6)

# Protocol 5 (stands for GNSS receiver) and velocity of communication SERIAL1_PROTOCOL 5

SERIAL1_BAUD 115

# Serial 2 (following the order in hwdef, it is USART 2)

# Protocol 1 (stands for telemetry) and velocity of communication SERIAL2_PROTOCOL 1

SERIAL2_BAUD 57

# Serial 3 (following the order in hwdef, it is USART 3)

# Protocol 5 (stands for GNSS receiver) and velocity of communication SERIAL3_PROTOCOL 5

SERIAL3_BAUD 115

# Serial 4 (following the order in hwdef, it is UART 7)

# Protocol 23 (stands for RCIN)

SERIAL4_PROTOCOL 23
SERIAL4_OPTIONS 0

# Serial 5 (following the order in hwdef, it is UART 8)

# Protocol 1 (stands for telemetry) and velocity of communication SERIAL5_PROTOCOL 1

SERIAL5_BAUD 57

# DroneCAN and CAN driver

CAN_D1_PROTOCOL 1
CAN_P1_DRIVER 1

# Disable safety pin (safety pin usually is required in some special boards) # Delay 3 ms to wait sensor response

BRD_SAFETYENABLE 0
BRD_BOOT_DELAY 3000

# Battery configuration for HEX Cube Power Brick BATT_MONITOR 4

BATT_VOLT_MULT 10.1
BATT_AMP_PERVLT 17.0

# IMU and compass orientation AHRS_ORIENTATION 0

COMPASS_ORIENT 0

## CHAPTER 4. SPACE APPLICATIONS AND REQUERIMENTS

This chapter investigates potential aerospace applications for drones and presents a preliminary analysis of the designed board, focusing on the microcontroller's radiation tolerance and its resilience against SEUs (Single Event Upset).

It is recommended to consult ANNEX-2, where Western industrial space standards have been overviewed, as well as the space environment for drones.

### 4.1. Space Applications

In outer space, there are few sites where a UAV (Unmanned Aerial Vehicle) can be flown easily. Being an aircraft without a human pilot, a UAV requires a significant amount of atmosphere to operate. The term “drone” can describe an unmanned vehicle used in different environments such as ocean, air, terrain, or space. Despite this versatility, only surface aerial vehicles are studied in this project.

Some of the solid-surface environments where aerial drones can operate are listed below. While other bodies exist, these are the primary candidates where a UAV, with specific modifications, could be deployed.

There are multiple possible applications. As mentioned previously, it is mandatory to fly the vehicle in an atmosphere environment to consider it as a UAV. Some of them can be:

- Applications inside the ISS:
The drone can be used as a supporting entity inside the ISS to monitor data, evaluate the environment, and assist with daily tasks.

This application was demonstrated by the Int-Ball (Internal Ball Camera) drone, created by JAXA. The experiment's objective was to evaluate the perspective inside the ISS and reduce the astronauts' workload, establishing a direct connection to ground stations.

Other possibilities include environmental monitoring and hazard mitigation, such as detecting fires or damage from space debris impacts and acting upon them. The biggest constraint in this scenario is the thermal dissipation of the drone's electronics.

- Applications in planet atmospheres:
- Mars: The first drone flying on this planet was the Ingenuity. Its mission was to scan the environment, map it, and evaluate the best route for the Perseverance rover.

The biggest constraints found were the low air density, pressure, and extreme temperature changes during day-night cycles (thermal cycling).

Currently, NASA is developing new drones to operate inside the Mars atmosphere.

There are other applications for the use of drones, such as: transport of goods, collection of samples in difficult access zones, non-static meteorological stations, and acting as transmitters of information between stations.

- Venus and Titan: In the case of Venus, the biggest drawbacks are the extreme pressure, temperature and corrosion. While applications similar to Mars were considered, these constraints prevent surface operations. VAMP (Venus Atmospheric Maneuverable Platform) is a concept drone designed to fly at an altitude of 50-65 km (a layer with more favorable conditions) for data acquisition, such as mapping, radiation analysis, and atmospheric study.

In the case of Titan, a drone mission is much more feasible. Scheduled for 2028, NASA plans to send a drone named Dragonfly to search for organic components. The main constraint on Titan is the extremely low ambient temperature. Similar to previous examples, multiple purposes are sought: mapping, geologic exploration, sample extraction and analysis.

### 4.2. Spenvis Radiation Simulations and PCB Changes

To obtain space environment data, the SPENVIS program [33] developed by ESA was used. Due to scope constraints, only Earth and Mars evaluations were considered. All simulations have been performed using an estimated mission duration of 2 years. As the solar activity period varies with time (11.2 year cycle), all analyses have been calculated starting from January 1, 2026, to align with high solar activity.

The main COTS (Commercial-off-the-shelf) components analyzed are:
- Primary component STM32H743VIT6 processor .
- Secondary components:
- Drone sensors: ICM20602, BMI088, BMP388 and BMM150.

The TID (Total Ionizing Dose) evaluation was performed using the Shieldose-2 model, considering a silicon target and aluminium shielding.

Defining the input parameters for long/short-term SEU has been a complex task and it is a mere approximation. Due to absence of specific radiation test data for the STM32H743VIT6. Since the STM32H7 relies on a 40 nm CMOS process, the sensitive volume approximated to 0.2 µm x 0.2 µm x 0.2 µm, this approximation is coherent with current 40 nm processors (typically x5, in other words: 40nm x 5 = 200 nm = 0.2 µm) [34].

The parameters chosen for the Weibell function are:
- 1 MeV·cm : As it is not a hardened device, this low threshold assumes

2
/mg
high sensitivity to ionizing particles.

- 5·10 | : This saturation cross-section corresponds to the typical ⁻⁸
cm

2
/bit
physical area of an SRAM cell in 40 nm technology.
- W = 80 and S = 1: Generic Weibell curve.

Regarding proton induced upset rates, the model used has been the Bendel function with standard values A = 12 MeV and B = 7.09 MeV, standard values for generic silicon with 40 nm.

### 4.2.1. LEO (Low Earth Orbit) Radiation

One of the worst LEOs is the SSO (Sun-Synchronous Orbit). This orbit is affected by the SAA (South-Atlantic Anomally), the fluence of protons and electrons from north and south poles by the magnetic field and the general outer space radiation from SPEs (Solar Particle Events) and GCRs (Galactic Cosmic Rays). The chosen orbital parameters are the 700 km height (semi-major axis 7078 km), 0º of eccentricity, 98º of inclination. Additional parameters are not considered important for these simulations. This was chosen to replicate the worst case scenario that the ISS orbit would experience.


Fig. 4.1 LEO Shieldose-2 results (same plot)

The maximum TID (Total Ionizing Dose) demonstrated and documented for STM32H753 is 47 krad, (version H743 is practically identical, [35]). To withstand this radiation level during 2 years of mission and a RDM (Radiation Design Margin) of 2, the maximum radiation environment should not exceed 23.5 krad.

A minimum of 0.5 mm of aluminum shielding satisfies this requirement. However, for structural and safety reasons, thicknesses of 2 mm and 4 mm have been implemented, obtaining a total dose of less than 5 krad for the complete mission.

For the calculation of SEU (Single Event Upsets): AP-8 (protons), SAPPHIRE-SPEs, ISO-15390-GCR and CREME-96 models are considered. The STM32H743 contains 1MB of RAM (main focus as it is volatile and sensitive). This 1MB contains 1048576 bytes of data, in other words, 8388608 bits. The calculation of the SEUs is using the following formula:

SEU | (4.1) device = SEUspenvis
·Number of bits

Long-term SEU simulations consider the total mission life with average radiation values. For 2 mm of aluminum is 910 errors, while for 4 mm is 246 errors (along 2 years).

Table 4.1-2: Long-term SEU for 2-4 mm of Al

Short-term SEU represents the worst-case simulation scenario, where a high amount of radiation interacts with the device over a short period. Considering the data in the table below and the microcontroller's memory size, a 2 mm shield would create 1653 errors per day, while using a thickness of 4 mm reduces this to around 451 SEUs per day.

Table 4.3: Short-term SEU for 2 mm of Al

Table 4.4: Short-term SEU for 4 mm of Al

This discrepancy between both values long and short terms is coherent, it exposes that during the mission the errors will be reduced but when a dangerous SPE occurs, the number of SEUs can be increased drastically. A short event can be more dangerous than the whole microcontroller life in the entire mission. This discrepancy requires protection strategies like watchdogs, ECC and redundancy.

To avoid these problems STM32H743 contains ECC (Error Correction Code), CRC (Cyclic Redundancy Check), IWDG (Independent Watchdog), WWDG (Window Watchdog) and MPU (Memory Protection Unit). Despite these commercial grade methods, it seems that the STM32 can resist these conditions with possible reboots but real test data and further research is necessary to confirm these aspects with possible degradation over time.

Moreover as a curiosity it is possible to plot radiation flux vs LET (Linear Energy Transfer) in short and long term SEU in Spenvis. When higher LET, less fluence we obtain, which is coherent.


Fig. 4.2 Fluence vs LET with 4 mm Al (Left→Short-term) (Right→ Long-term)

### 4.2.2. Mars Radiation

Since the Martian surface cannot be simulated with SPENVIS, the closest circular orbit considered is at an altitude of 100 km, with an inclination of 98º. In this environment the atmosphere and magnetic attenuation is minimum compared to the Earth. AP-8 and AE-8 models are not required because protons and electrons are not trapped as in Van-Allen belts (they don’t exist), reducing these sources of radiation. The models that have been considered are SAPPHIRE for SPEs, ISO-15390 for GCR and CREME-96 to simulate.

Fig. 4.3 Mars Shieldose-2 results (same plot)

Using Shieldose-2, the minimum thickness of aluminum should be 0.02 mm for 23.5 krad. For structural and safety reasons 2 and 4 mm of aluminium have been considered, obtaining less than 5 krad.

In case of long-term SEU simulation, the number of errors is 2858 for 2 mm and 761 for 4 mm of aluminum.

Table 4.5-6: Long-term SEU for 2-4 mm of Al

In case of short-term SEU simulation, the number of errors per day is 3235 for 2 mm and 614 for 4 mm of aluminum.

Table 4.7: Short-term SEU for 2 mm of Al

Table 4.8: Short-term SEU for 4 mm of Al

It is coherent to encounter more TID (Total Ionizing Radiation) at LEO orbit than on Mars, due to the high flux of trapped protons-electrons in the Van Allen belts and the SAA (South Atlantic Anomaly). On the other hand, we have more SEUs on Mars, due to the absence of geomagnetic shielding, exposing the device to the unattenuated spectrum of GCR (high-LET ions), which are the primary drivers of SEU in deep space.

In conclusion, the protection strategy must be adapted to the orbit: while physical shielding is the critical countermeasure for LEO to mitigate TID, it is less effective against high-energy particles in the Martian environment. Therefore, Mars missions rely mainly on active mitigation (redundancy, ECC mechanisms) to maintain stability against frequent errors.

### 4.2.3. Conclusion of PCB, COTS and general changes

- Regarding COTS (Commercial-off-the-shelf) components: A rigorous qualification and selection process is mandatory. Since components usually contain distinct internal structures ranging from pure silicon dies to mechanical vibrating elements. These shall operate well below their rated limits to reduce stress and extend operational life (derating). To mitigate outgassing risks, a thermal vacuum bake-out campaign is mandatory prior to integration.

Redundancy is a must in this type of missions; heterogeneous redundancy, LCL (Latch-up Current Limiters), and software redundancy are common techniques. All components shall work inside the operating temperature and pressures and always placed near mounting points with staking (epoxy) to withstand accelerations and vibrations. In LEO, the primary challenge is heat dissipation due to the vacuum, while Mars requires active heating to prevent component freezing.

Typical drone components like the BMM150 (magnetometer) can measure the magnetic field in LEO conditions, its resolution is capable of doing so. In the case of the BMP388 (barometer) it won’t work in LEO and on Mars. It would be able to evaluate the environment only if it is inside the ISS or during launch phase. Filling critical structures with SF6 gas can suppress arcing (and could be monitored by the BMP388), it adds structural complexity. Therefore, solid potting or conformal coating is selected as the primary mitigation strategy against arcing and corona effects.

- Regarding PCB design and materials: A high-Tg material such as a special FR-4 and epoxy substrate is selected to ensure mechanical stability. To optimize thermal dissipation and structural integrity, the layout should incorporate thermal vias, teardrop connections, continuous ground planes (inner and outer), and maximize copper pours.

To mitigate tin whiskers it is mandatory to use SnPb solder. For surface finish, ENIG (Electroless Nickel Immersion Gold) is preferred over HASL (Hot Air Solder Leveling) due to its superior resistance to corrosion and atomic oxygen, due to gold being non-reactive.

To protect against ESD (Electrostatic Discharge), TVS space grade diodes are considered. Spark gaps are not effective in void conditions, and for low pressure atmospheres they can produce short circuits as their basis is on Paschen law. To avoid arcing and coronas effect, copper connection shall be rounded and never perpendicular or sharp edges. Lastly, a conformal coating is required to prevent electrical arcing, protect against conductive debris, and mitigate thermal stress.

- Note: Sharp edges are prohibited in electronics because they concentrate the electric field, causing uncontrolled corona discharges and arcing. However, on the spacecraft exterior, this effect is useful. Tungsten needles are installed to intentionally bleed off static charge via field emission, preventing high-voltage accumulation that could damage the solar panels.

## CHAPTER 5. TESTS, ISSUES, COST AND ENVIRONMENT

This chapter details from a broad perspective, the performed tests with the designed flight controller, the resolved and remaining issues, the cost of the prototype's production, as well as its environmental and social impacts.

### 5.1. Tests and issues

The developed board was validated using a custom 3D printed case integrated into a Hexsoon EDU 450 drone frame, equipped with a Here4 (GNSS and magnetometer), radio receiver, and telemetry module. All peripherals were connected via standard Pixhawk connectors. 3 flight tests were conducted in Loiter mode: an anchored safety test, a free flight within a geofence, and an autonomous 4 waypoint mission. The board demonstrated excellent stability and full functionality in all tests.

Additionally, the direct power connection was tested using a 24 V power supply with no issues. However, specific requirements were identified: a 24 MHz HSE (High Speed External oscillator) is mandatory for firmware compatibility, and ESD protection improvement on specific buses. During testing, continuous handling caused an electrostatic discharge that damaged the oscillator, requiring its replacement. Moreover, the onboard magnetometer could not be calibrated due to environmental noise, and MicroSD communication remained inactive, likely due to a configuration conflict in hwdef.dat or hardware crosstalk.


Fig. 5.1 Left→ First test with anchor, Right→ Second test within a geofence

For more information check ANNEX-3: Testing, Project Issues, Comparison and Cost.

### 5.2. Hardware budget

The cost of manufacturing the boards is shown in the following table:

Table 5.1: Prototype cost
Object: | Cost with taxes:
JLCPCB production This contains: - 5 boards (2 mounted) - 1 stencil board | 344.04 €: - 227.29 € material - 116.75 € tariffs
3 extra clocks to substitute | 27 €
3D printed case material and screws | 2.5 € approx
Total approx: | 373.54 €

This is only a rough approximation. Unit costs are higher during prototyping but decrease significantly when manufactured at scale.

While the prototype unit cost is 186.77 €, mass production would drop the price to 65-85€ approx compared with direct competitors, which typically oscillate between 90 € and 160 €. For instance: MATEK H743 90-120€, Holybro Kakute H7 v2 120 €, and the Holybro Pixhawk 6C Mini 150 €. Specialized industrial variants like the mRo Control Zero 280 € or CUAV Nora+ 220 € represent a higher price.
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

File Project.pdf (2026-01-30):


14/12/2025

Project Project
Configuration Report

## 1. Description

### 1.1. Project

Project Name | Project
Board Name | custom
Generated with: | STM32CubeMX 6.15.0
Date | 12/14/2025

### 1.2. MCU

MCU Series | STM32H7
MCU Line | STM32H743/753
MCU name | STM32H743VITx
MCU Package | LQFP100
MCU Pin number | 100

### 1.3. Core(s) information

Core(s) | ARM Cortex-M7

## 2. Pinout Configuration


## 3. Pins Configuration
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

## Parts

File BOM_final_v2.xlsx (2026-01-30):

Comment | Description | Designator | Footprint | LibRef | Quantity | LSCS part #
BMP388, | P-Sensor SPI I2C 1, 25 Bar SMD | BAR | PQFN50P200X200X80-10N | BMP388 | 1 | C779278
100nF 1mOhm, | CAP CER 0.1UF 16V X7R 0402 | BMIC1, BMIC2, BMMC1, BMMC2, BMPC1, BMPC2, BOOTC1, CANC1, CANC3, HSEC1, ICMC1, ICMC4, NRST_C1, POWC1, POWC2, POWC3, SDC1, STC5, STC6, STC7, STC8, STC9, STC10, STC11, STC12, STC13, USBC1, USBC2, USBC4, V5C3 | FP-GRM15-MFG | CMP-2100-03641-2 | 30 | C71629
TPD2E2U06DRLR, | TVS DIODE 5.5V 12.4V SOT5 | BMIU1, BMIU2, BMIU3, DEU1, DEU2, GPS1U1, GPS2U1, I2CEU1, I2CU1, ICMU1, ICMU2, RCINU1, SDU1, SDU2, SDU3, SPIEU1, SPIEU2, SPIEU3, TELEM1U1, TELEM2U1, USBU1 | FP-DRL0005A-MFG | CMP-04985-000005-1 | 21 | C1972959
SSAJ120100, | Switch | BOOT, NRST | SSAJ120100 | SSAJ120100 | 2 | C160864
10kOhm, | Resistor, Resistor 10kohm 0402WGF1002TCE | BOOTR1, NRSTR, SDR1, SDR2, SDR3, SDR4, SDR5, USBR4 | RESC1608X55N | 0603WAF1002T5E | 8 | C25804
SM04B-GHS-TB(LF)(SN), | CONN HEADER SMD R/A 4POS 1.25MM | CAN, I2C | FP-SM04B-GHS-TB_LF_SN-MFG | CMP-17439-000411-1 | 2 | C189895
2.2uF, | Cap Ceramic 2.2uF 6.3V X5R ±20% SMD 0402 +85°C Paper T/R | CANC2, CANC4, ICMC2, USBC3, VCAP1, VCAP2 | FP-CL50-IPC_C | CMP-13271-001039-1 | 6 | C12530
120Ohm, | Resistor | CANR1 | RESC1608X55N | 0603WAF1200T5E | 1 | C22787
TJA1051TK/3/1J, | IC TRANSCEIVER HALF 1/1 8HVSON | CANU1 | FP-SOT782-1-MFG | CMP-10098-000001-1 | 1 | C2875699
BMM150, | SENSOR FLIPCORE/HALL SPI 12WLCSP | COMP | FP-BMM150-MFG | CMP-191063-000001-2 | 1 | C171681
SM06B-GHS-TB(LF)(SN), | CONN HEADER SMD R/A 6POS 1.25MM | DEBUG, GPS, GPS2, TELEM1, TELEM2 | FP-SM06B-GHS-TB_LF_SN-MFG | CMP-17439-000061-1 | 5 | C133065
HTSW-110-07-L-T, | Connector | Headers | HDRV30W64P254_3X10_2540X756X838P | HTSW-110-07-L-T | 1 | C7286350
SIT1602AI-22-33E-26.000000D, | No Description Available | HSE | SON4_SIT1602-2_SIT | SIT1602AI-22-33E-26.000000D | 1 | C30103
2.2kOhm, | Resistor | HSER1, I2CER1, I2CER2, I2CR1, I2CR2, POWR1, POWR2 | RESC1608X55N | 0603WAF2201T5E | 7 | C4190
10nF, | Cap Ceramic 10nF 50V X7R ±10% SMD 0402 +125°C Paper T/R | ICMC3 | FP-CL165-IPC_C | CMP-13271-000387-1 | 1 | C15195
ICM-20602, | High Performance 6-Axis MEMS MotionTracking(TM) Device, 1.71 to 3.45 V, -40 to 85 degC, 16-Pin LGA, RoHS | IM1 | INSE-I62-16 | CMP-2000-07589-1 | 1 | C97633
BMI088, | High-performance 6-axis inertial sensor (accelerometer + gyroscope) | IM2 | PQFN50P450X300X100-16N | 0 | 1 | C194919
SIT1552AI-JE-DCC-32.768D, | MEMS OSC TCXO 32.7680KHZ LVCMOS | LSE | FP-SiT1552-J-MFG | CMP-25159-264721-1 | 1 | C367054
1uF, | Cap Ceramic 1uF 25V X5R ±10% SMD 0402 +85°C Paper T/R | POWC4, SDC2, STC1, STC2 | FP-CL542-IPC_C | CMP-13271-001051-1 | 4 | C52923
502494-0670, | Connector | POWER | 5024940670 | 502494-0670 | 1 | C587930
104031-0811, | Surface Mount Micro SD Card Connector, with Push In Termination | SD | MOLEX_104031-0811 | 104031-0811 | 1 | C585350
SM07B-GHS-TB(LF)(SN), | CONN HEADER SMD R/A 7POS 1.25MM | SPI | FP-SM07B-GHS-TB_LF_SN-MFG | CMP-17439-000109-1 | 1 | C495552
STM32H743VIT6, | IC MCU 32BIT 2MB FLASH 100LQFP | ST | FP-LQFP100-1L-MFG | CMP-12105-000050-1 | 1 | C114409
4.7uF, | Cap Ceramic 4.7uF 10V X5R ±20% SMD 0402 +85°C Paper T/R | STC3, STC4 | FP-CL282-IPC_C | CMP-13271-000548-1 | 2 | C23733
TYPE-C-31-M-12, | USB Connectors 24 Receptacle 1 8.94*7.3mm RoHS | USB | HRO_TYPE-C-31-M-12 | TYPE-C-31-M-12 | 1 | C165948
SMBJ5.0A, | TVS DIODE 5V 9.2V DO214AA | USBD1, V5D2 | FP-SMBJ-MFG | CMP-08607-000042-1 | 2 | C83333
5.1kOhm, | Resistor | USBR1, USBR2, USBR3 | RESC1608X55N | 0603WAF5101T5E | 3 | C23186
4.7uF 3mOhm, | Chip Multilayer Ceramic Capacitors for General Purpose, 1206, 4.7uF, X7R, 15%, 10%, 50V | V5C1in | FP-GRM31C-0_2-e0_3_0_8-IPC_C | CMP-1037-04923-3 | 1 | C77096
100nF 39mOhm??, | Chip Multilayer Ceramic Capacitors for General Purpose, 0402, 0.10uF, X7R, 15%, 10%, 50V | V5C2in, V5DivC | FP-GRM155-0_05-IPC_B | CMP-2008-04639-2 | 2 | C77020
47uF 3mOhm, | CAP CER 47UF 16V X5R 1210 | V5C4, V5C5, V5C6 | FP-GRM32E-0_3-0_2-IPC_C | CMP-2000-06362-2 | 3 | C77101
SMBJ36A, | TVS DIODE 36V 58.1V DO214AA | V5D1 | FP-SMBJ-MFG | CMP-08607-000022-1 | 1 | C224020
360kOhm 100mW, | Resistor | V5Div1 | RESC1608X55N | RC0603FR-07360KL | 1 | C137740
30.9kOhm 63mW, | Resistor | V5Div2 | RESC1005X40X25LL05T05 | CMP-2002-08508-1 | 1 | C2085168
3425L300_36MR, | Fuse | V5F1 | FUSC8664X140N | 3425L300_36MR | 1 | C20349218
LMR51450FNDRRR, | Integrated Circuit | V5IC1 | SON50P300X300X80-13N-D | LMR51450FNDRRR | 1 | C5782413
10uH 16mOhm, | Power Inductor, 10 uH, +/- 20%, -40 to 100 degC, 2-Pin SMD, RoHS, Tape and Reel | V5L1 | SUMI-CDRH127_V | CMP-2000-06084-1 | 1 | C2452998
SI7489DP-T1-E3, | MOSFET P-CH 100V 28A PPAK SO-8 | V5Q1 | FP-S17-0173-SINGLE-MFG | CMP-02550-000038-1 | 1 | C141576
AC2512JK-070RL, | Resistor | V5R0, V31R0, V32R0 | RESC6431X65N | AC2512JK-070RL | 3 | C144428
100kOhm, | Resistor | V5R1, V5R3, V5R4, V31R1, V32R1 | RESC2013X65N | 0805W8F1003T5E | 5 | C149504
30.9kOhm, | Resistor | V5R2 | RESC1005X40X25LL05T05 | CMP-2002-08508-1 | 1 | C2085168
16.9kOhm, | RES Thick Film, 16.9kO, 1%, 0.063W, 100ppm/°C, 0402 | V5R5 | FP-CRCW0402-e3-MFG | CMP-2002-08240-2 | 1 | C481959
SS34C, | Schottky Diode | V5S1 | DIOM7959X262N | SS34C | 1 | C13763
BZT52C15-E3-08, | Zener Diode | V5Z1 | SOD3716X135N | BZT52C15-E3-08 | 1 | C2104
10uF 3mOhm, | CAP CER 10UF 10V X5R 0805 | V31C1, V32C1 | FP-C0805C-DG-MFG | CMP-2007-03243-2 | 2 | C2167673
390pF 1mOhm, | CAP CER 390PF 50V X7R 0603 | V31C2, V32C2 | FP-CC0603-DA-MFG | CMP-03422-000674-1 | 2 | C107089
22uF 1mOhm, | Capacitor | V31C3, V32C3 | CAPC1608X90N | GRM188R60J226MEA0D | 2 | C77042
2.2uH, | Inductor | V31L1, V32L1 | INDPM4042X200N | PA4332.222NLT | 2 | C3222957
TPS62142RGTT, | Buck Step Down Regulator with 3 to 17 V Input and 3.3 V Output, -40 to 85 degC, 16-Pin QFN (RGT), Green (RoHS & no Sb/Br) | V31U1, V32U1 | RGT0016C_V | CMP-0323-00127-3 | 2 | C2070653

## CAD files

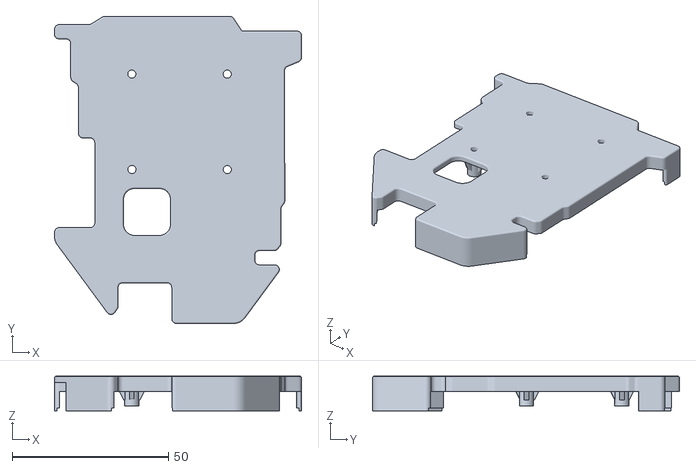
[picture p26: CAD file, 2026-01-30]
3D_case/pieza_top_completa.STL
79.0 x 98.2 x 11.1

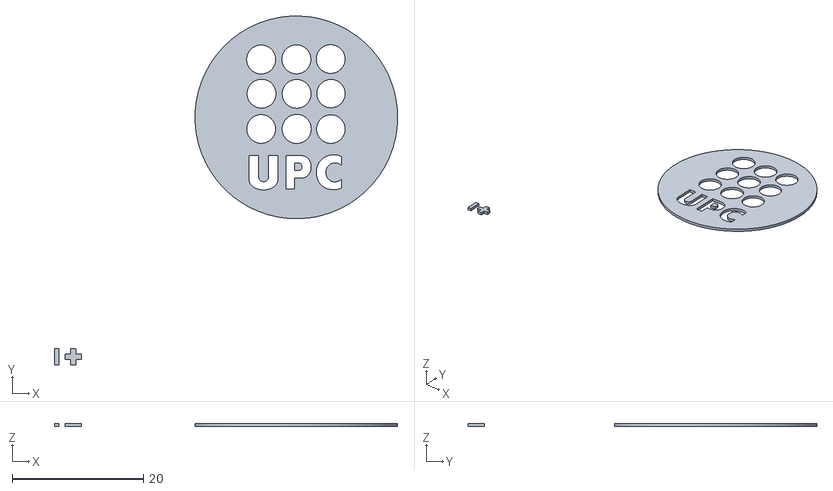
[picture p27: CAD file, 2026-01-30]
3D_case/pieza_top_partes.STL
52.3 x 53.1 x 0.5

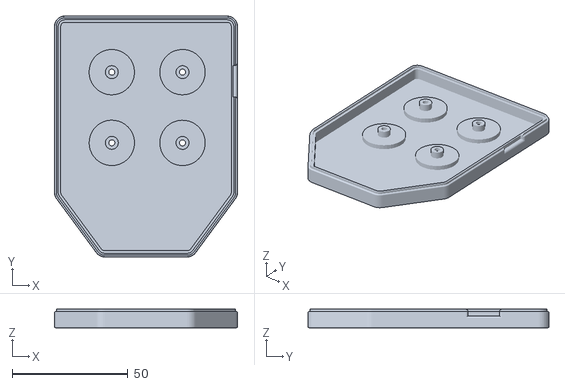
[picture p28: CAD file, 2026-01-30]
3D_case/pieza_bot.STL
79.0 x 104.0 x 8.00

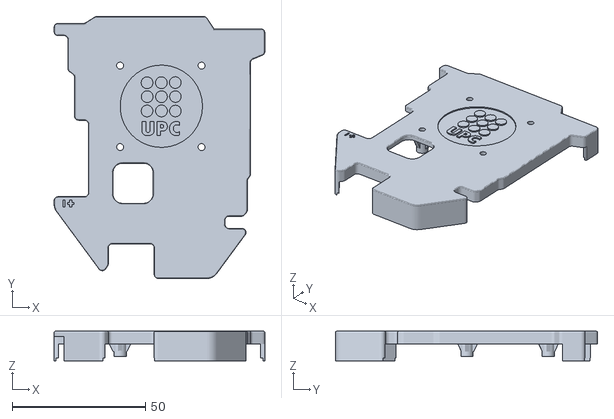
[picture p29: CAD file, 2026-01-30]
3D_case/pieza_top_1 (1).STL
79.0 x 98.2 x 11.1

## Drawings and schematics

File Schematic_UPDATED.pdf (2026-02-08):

# BAT REGULATOR 6-36V TO 5V 3A

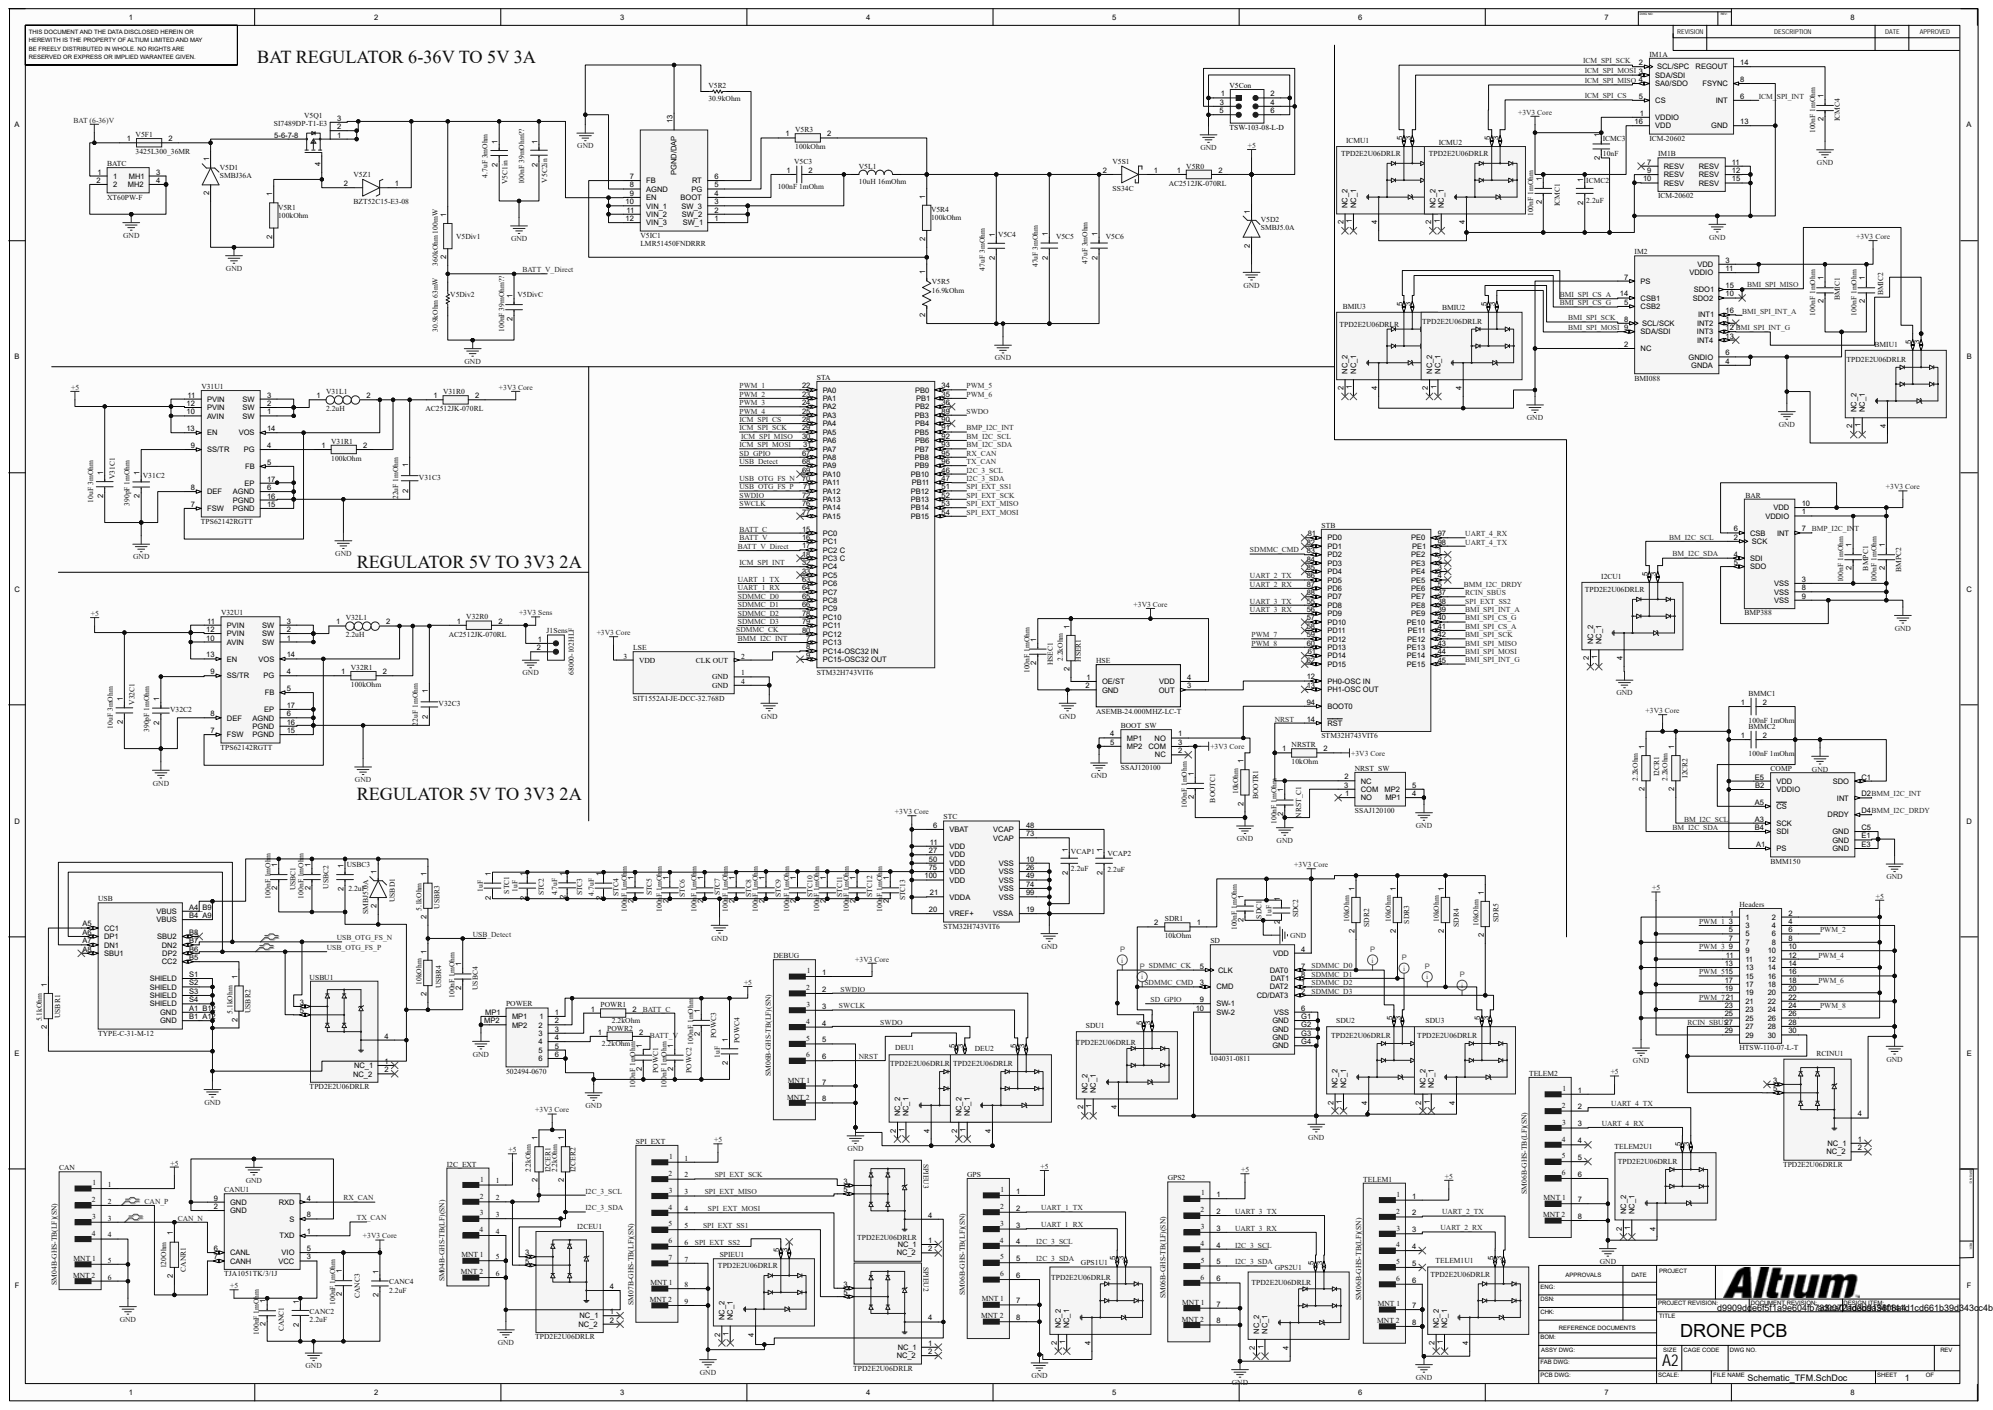
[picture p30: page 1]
DWG NO:; REV:; DRONE PCB; Schematic_TFM.SchDoc; TITLE; SIZE; DWG NO.; FILE NAME; SHEET; REV; SCALE:; CAGE CODE; PROJECT APPROVALS; DATE; ENG:; DSN:; CHK:; REFERENCE DOCUMENTS; BOM:; ASSY DWG:; FAB DWG:; PCB DWG:; PROJECT REVISION:; DOCUMENT REVISION:; DESIGN ITEM: d9909dde6f5f1a9e604fb733ca01fdebda3408a4 ad0072ad3d9198f141d1cd661b39d343cc4b; REVISION; DESCRIPTION; APPROVED; BAT (6-36)V; GND; BZT52C15-E3-08; 2 1 V5D1 SMBJ36A; 2 1 V5D2 SMBJ5.0A; LMR51450FNDRRR; 4.7uF 3mOhm; 47uF 3mOhm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

THIS DOCUMENT AND THE DATA DISCLOSED HEREIN OR
HEREWITH IS THE PROPERTY OF ALTIUM LIMITED AND MAY
BE FREELY DISTRIBUTED IN WHOLE. NO RIGHTS ARE
RESERVED OR EXPRESS OR IMPLIED WARANTEE GIVEN.

1 2 V5R1 100kOhm SW_1 1 SW_2 2 SW_3 3 BOOT 4 PG 5 RT 6 PGND/DAP 13 VIN_3 12 VIN_2 11 VIN_1 10 EN 9 AGND 8 FB 7 V5IC1

100nF 1mOhm VDD 3 CLK OUT 2

SM06B-GHS-TB(LF)(SN) PWM_8 PWM_7

SM06B-GHS-TB(LF)(SN)

DWG NO: REV:

SM04B-GHS-TB(LF)(SN)

SM07B-GHS-TB(LF)(SN)

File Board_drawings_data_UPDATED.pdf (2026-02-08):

A

B

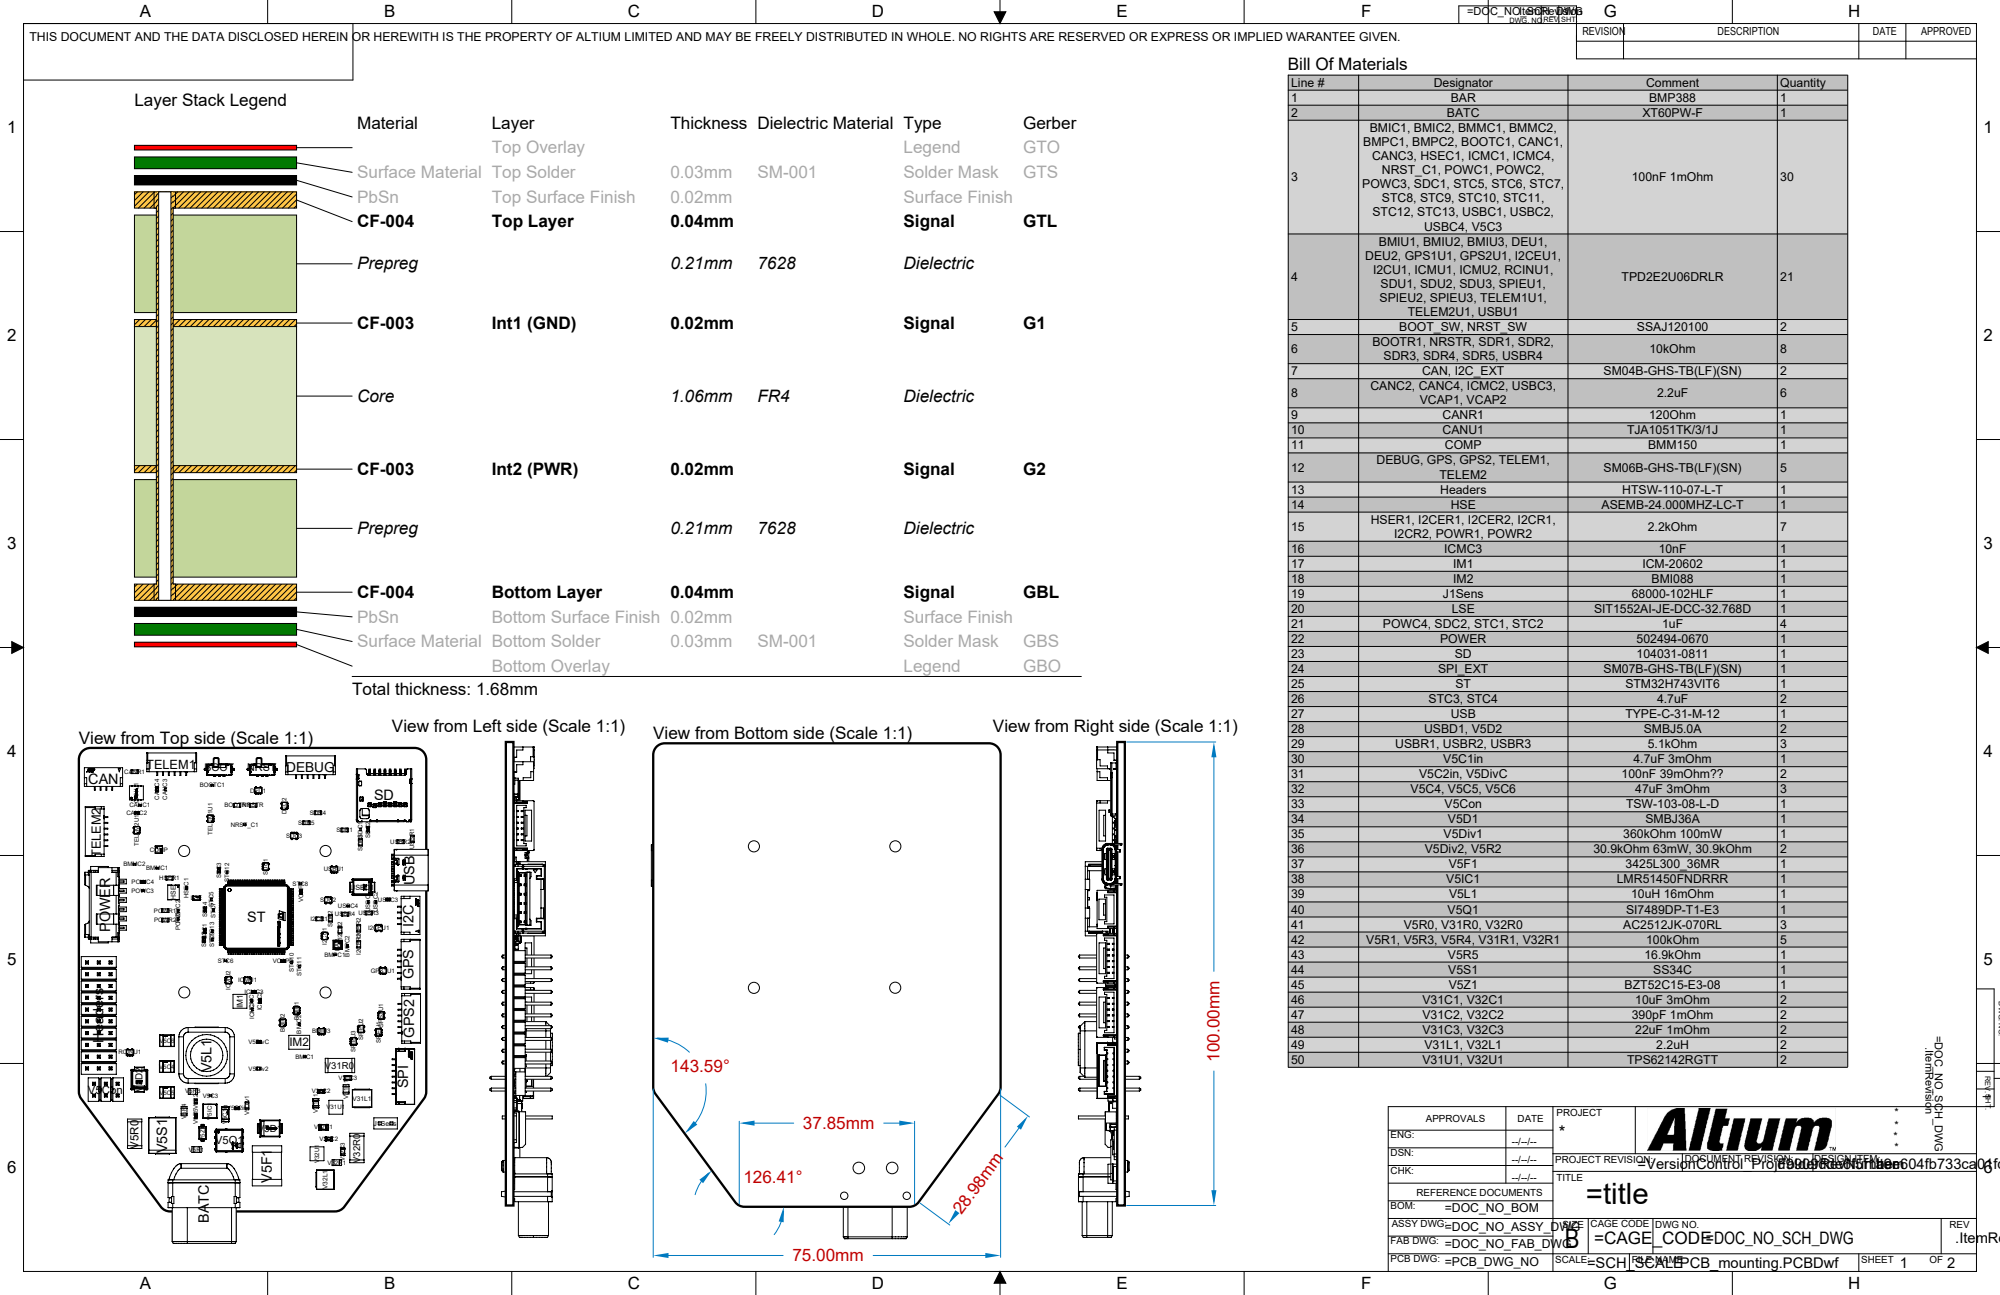
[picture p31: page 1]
6 USB BATC V5C3; USBC4; USBC1; USBC2; STC8; STC6; SDC1; POWC3; POWC2 POWC1; NRST_C1ICMC⁴ ICMC¹; HSEC1; CANC3; CANC1; BOOTC1; BMPC1; BMPC2; BMMC2; BMMC1; BMIC2; BMIC1; STC13; STC12; STC11; STC10; STC9 STC7STC5; V5Div2; NRSTR; USBR4; SDR5; SDR4; SDR3; SDR2; SDR1; BOOTR1V⁵Div1; USBR3; USBR2 USBR¹; POWR2; POWR1; I2CER2 I2CER1; HSER1; CANR1; V5DivC; VCAP1; VCAP2; USBC3; ICMC2; CANC4; CANC2; STC4; STC3; STC2STC1; SDC2; POWC4; ICMC3; COMP; SDU1; USBU1; RCINU1; GPS1U1; DEU1; BMIU3; TELEM2U1; SPIEU1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

DWG. NO.REV.SHT.

THIS DOCUMENT AND THE DATA DISCLOSED HEREIN OR HEREWITH IS THE PROPERTY OF ALTIUM LIMITED AND MAY BE FREELY DISTRIBUTED IN WHOLE. NO RIGHTS ARE RESERVED OR EXPRESS OR IMPLIED WARANTEE GIVEN.

Layer Stack Legend

SM04B-GHS-TB(LF)(SN)

SM06B-GHS-TB(LF)(SN)
HTSW-110-07-L-T
ASEMB-24.000MHZ-LC-T

A

B

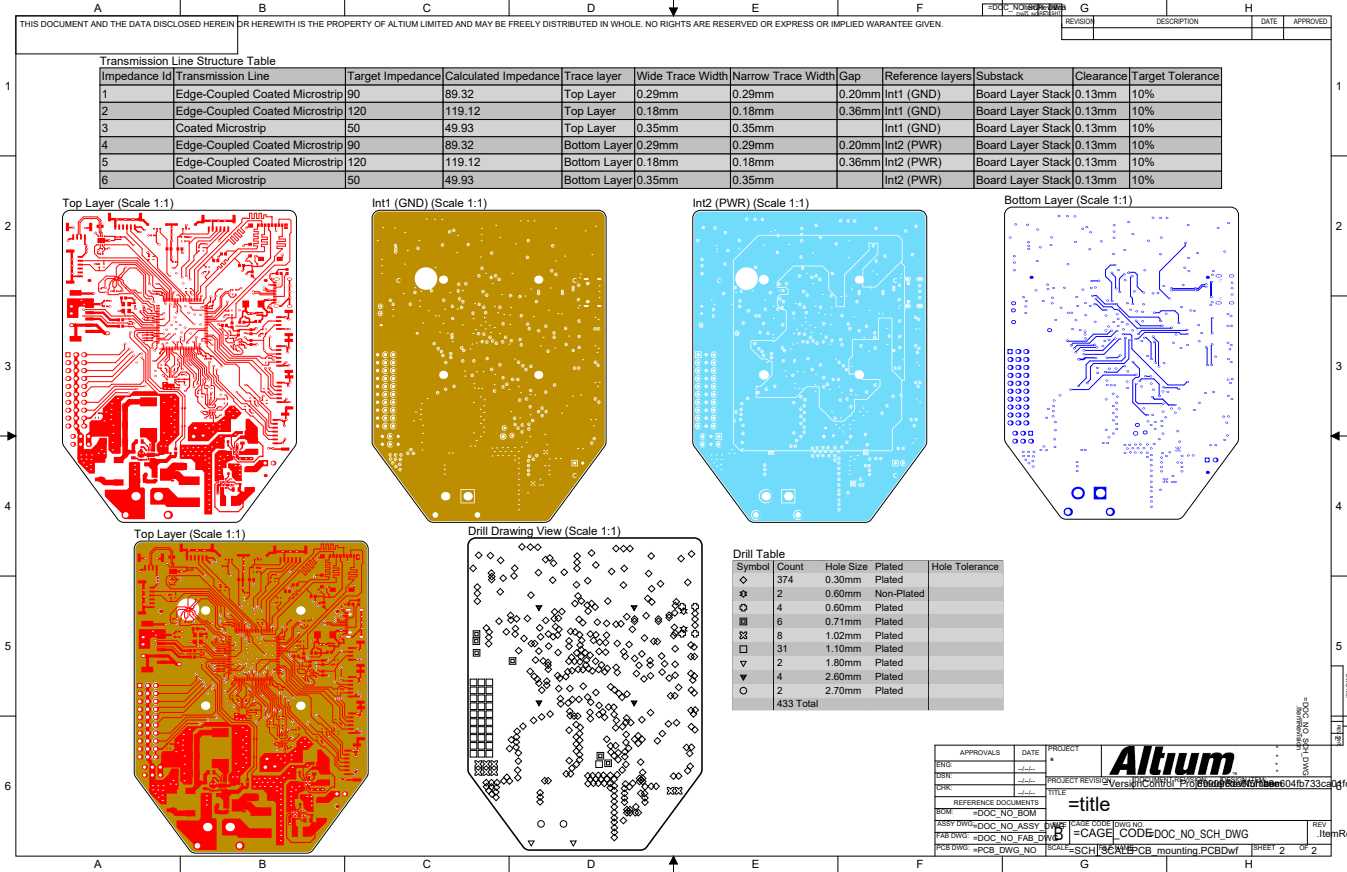
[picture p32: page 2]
Top Layer (Scale 1:1); Int1 (GND) (Scale 1:1); Int2 (PWR) (Scale 1:1); Bottom Layer (Scale 1:1); Drill Drawing View (Scale 1:1); Impedance Id 1 2 3 4 5 6; Target Impedance 90 120 50 90 120 50; Calculated Impedance 89.32 119.12 49.93 89.32 119.12 49.93; Trace layer Top Layer Top Layer Top Layer Bottom Layer Bottom Layer Bottom Layer; Wide Trace Width 0.29mm 0.18mm 0.35mm 0.29mm 0.18mm 0.35mm; Narrow Trace Width 0.29mm 0.18mm 0.35mm 0.29mm 0.18mm 0.35mm; Gap 0.20mm 0.36mm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

DWG. NO.REV.SHT.

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

Transmission Line
Edge-Coupled Coated Microstrip
Coated Microstrip

Substack
Board Layer Stack

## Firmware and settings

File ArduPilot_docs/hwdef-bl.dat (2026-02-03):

# hwdef-bl.dat - CustomH7 

MCU STM32H7xx STM32H743xx

OSCILLATOR_HZ 24000000
STM32_HSE_BYPASS
STM32_LSE_BYPASS


APJ_BOARD_ID 1001
USB_VENDOR 0x2DAE
USB_PRODUCT 0x1001
USB_STRING_MANUFACTURER "CustomH7"
USB_STRING_BOOTLOADER "CustomH7 Bootloader"


FLASH_SIZE_KB 2048
FLASH_RESERVE_START_KB 0
FLASH_BOOTLOADER_LOAD_KB 128
APP_START_OFFSET 0x20000


PA11 OTG_FS_DM OTG1
PA12 OTG_FS_DP OTG1
PA9  VBUS INPUT

PC6 USART6_TX USART6
PC7 USART6_RX USART6



PA4  ICM_CS       CS
PE11 BMI_ACCEL_CS CS
PE10 BMI_GYRO_CS  CS
PE8  EXT_CS1      CS
PB12 EXT_CS2      CS


SERIAL_ORDER OTG1 USART6


define CH_CFG_USE_MEMCORE 1
define CH_CFG_USE_HEAP 1
define CH_CFG_USE_SEMAPHORES 0
define CH_CFG_USE_MUTEXES 1
define CH_CFG_USE_DYNAMIC 1
define CH_CFG_USE_WAITEXIT 1
define CH_CFG_USE_REGISTRY 1


PC8  SDMMC1_D0  SDMMC1
PC9  SDMMC1_D1  SDMMC1
PC10 SDMMC1_D2  SDMMC1
PC11 SDMMC1_D3  SDMMC1
PC12 SDMMC1_CK  SDMMC1
PD2  SDMMC1_CMD SDMMC1
PA8  SD_DETECT  INPUT PULLUP


define HAL_OS_FATFS_IO 1

define AP_BOOTLOADER_FLASH_FROM_SD_ENABLED 1
